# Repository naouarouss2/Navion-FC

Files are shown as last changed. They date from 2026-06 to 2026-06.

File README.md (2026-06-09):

# Navion FC

## What is it
It is a small all-in-one flight controller used for autonomous vehicles.

It will run Ardupilot and is compatible with any type of autonomous vehicles.

## Features ✅
-  Barometer
-  IMU
-  Magnometer
-  10 PWM outputs
-  PPM/SBUS input
-  4 Neopixel outputs
-  MicroSD Card Reader
-  USB-C Connector
-  SWD Debugging Interface
-  3 UART Headers
-  1 USART Header
-  1 I²C Header
-  Safety Switch Header
-  16MB External Flash
-  Battery Voltage Monitoring
-  Up to 40V battery input voltage
## Why do I want to make it ? 🛠️

I have always been passionate about autonomous vehicles and wanted to build a universal solution that can run all of the vehicles I'll be building in the future.

That's why I made my flight controller extremely modular and versatile.

## How does it work ?

-  You attach all of your ESCs and Servos to the PWM outputs.

-  Attach neopixel strips to the top neopixel headers (You should power them externally).

-  Connect a standard Pixhawk 2.4.8 (or similar) GPS module (You need to swap the connectors for JST-XH connectors) to the GPS and I²C headers.

-  Connect the battery to the battery header.

-  Connect the RC receiver to the PPM/SBUS header (and configure it accordingly later).

-  Connect a telemetry module to the USART2 header.

-  You can connect other UART accessories like a Lidar to the UART2 and UART3 headers.

-  Then you configure your peripherals in **Mission Planner**, setup your flight controller, plan a mission, and you should be good to go !

## PCB 

### Schematic



### Routing



### 3D View



## 3D Deisgn 🎨





## Firmware

This flight controller will run a custom ported version of the **[Ardupilot firmware](https://github.com/ArduPilot/ardupilot)**

## Disclaimer ⚠️

This project is still untested.

## Credits ❤️
Project made by : **Oussama NAOUAR**

Total logged working hours : **40 hrs**

Made as part of the **Hack Club Fallout** program.

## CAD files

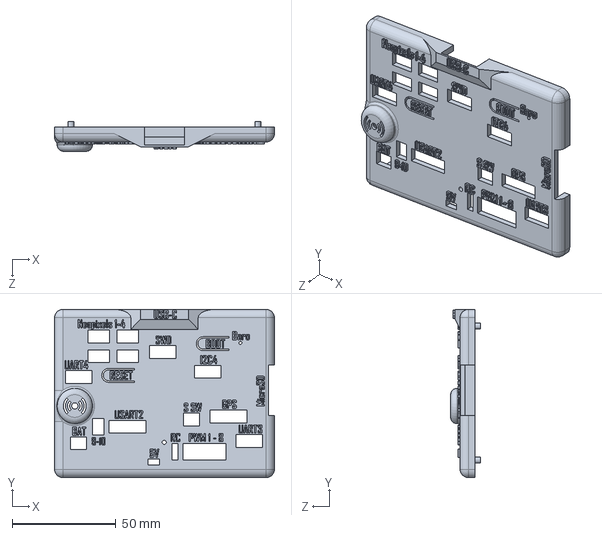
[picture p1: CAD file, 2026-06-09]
3D Printed Case/SolidWorks Files/Upper part.SLDPRT
106.0 x 81.0 x 14.3 mm

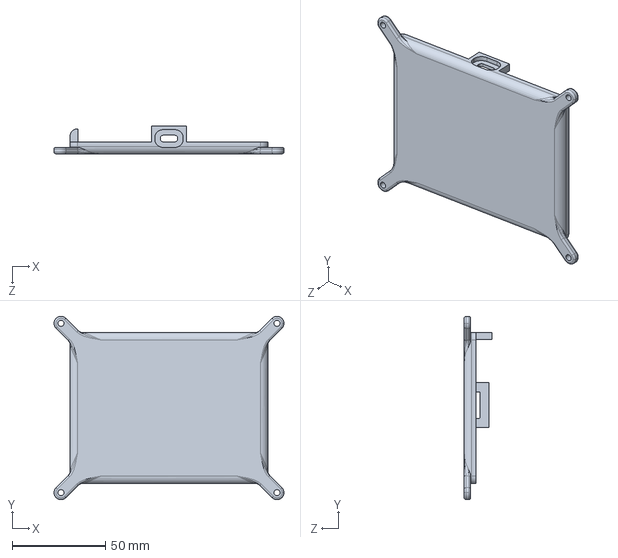
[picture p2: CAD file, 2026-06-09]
3D Printed Case/STEP Files/Lower part.STEP
123.2 x 98.2 x 14.8 mm

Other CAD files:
3D Printed Case/SolidWorks Files/Lower part.SLDPRT

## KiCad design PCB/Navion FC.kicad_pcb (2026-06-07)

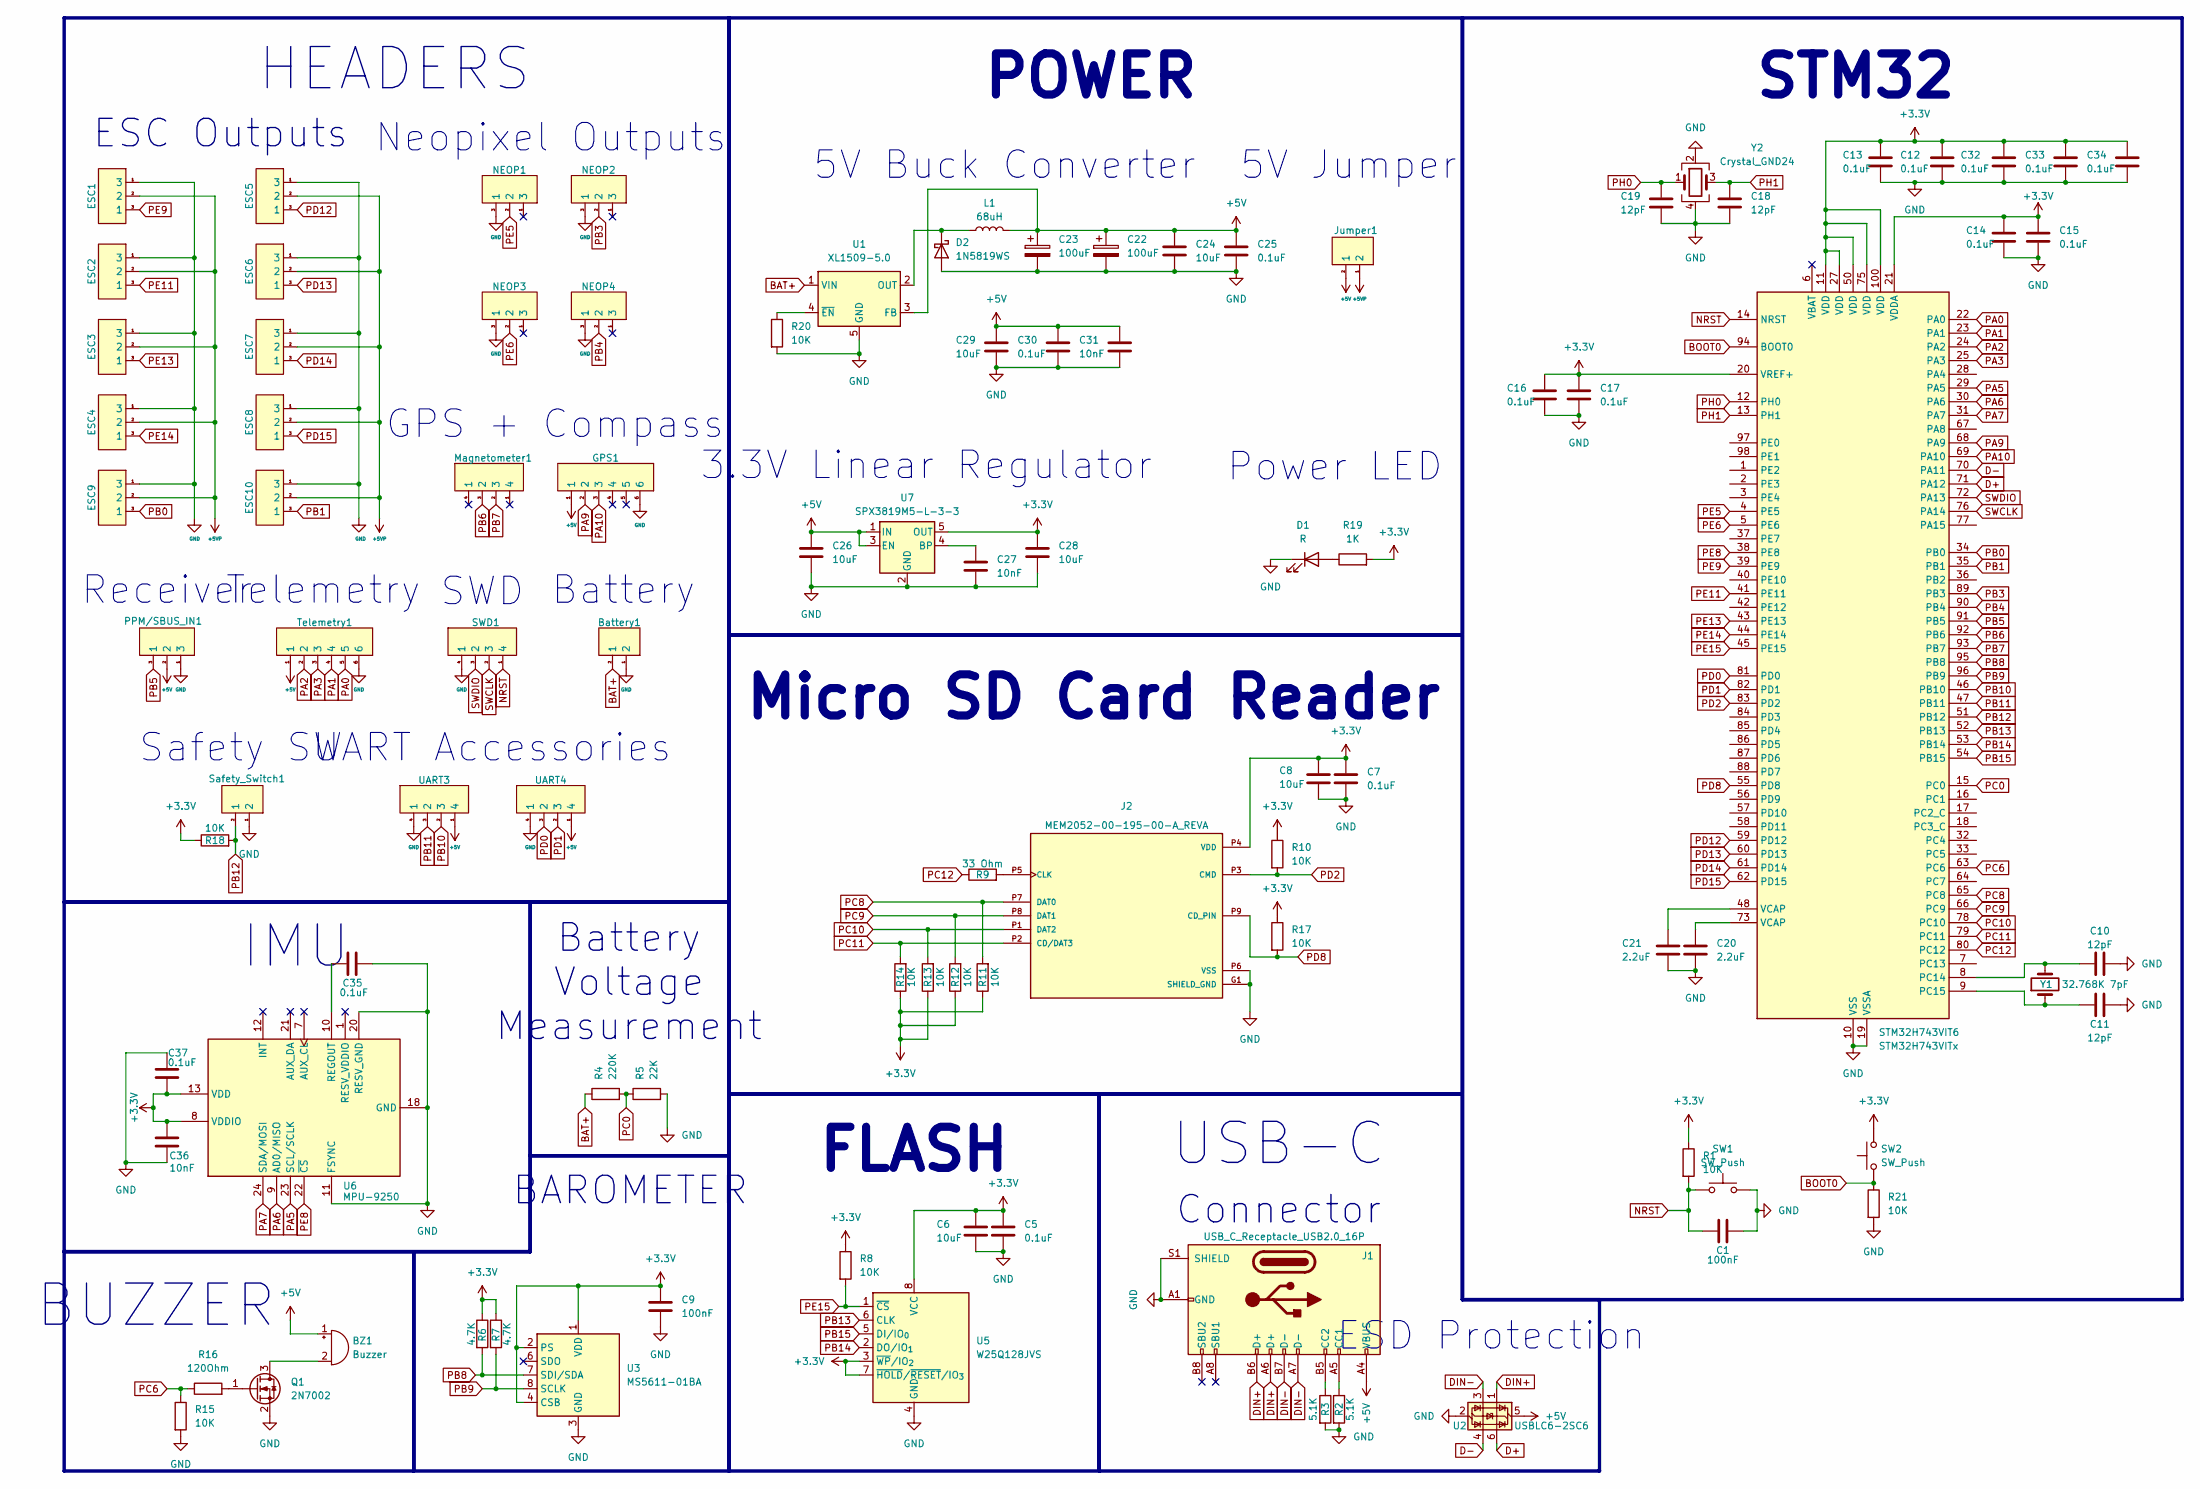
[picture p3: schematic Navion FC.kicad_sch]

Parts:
BZ1: Buzzer; Buzzer_12x9.5RM7.6
Battery1: JST_XH_B2B-XH-A_1x02_P2.50mm_Vertical
C1, C9: 100nF; C_0603_1608Metric
C5, C7, C12, C13, C14, C15, C16, C17, C25, C30, C32, C33, C34, C35, C37: 0.1uF; C_0603_1608Metric
C6, C8, C24, C26, C28, C29: 10uF; C_0603_1608Metric
C10, C11, C18, C19: 12pF; C_0603_1608Metric
C20, C21: 2.2uF; C_0603_1608Metric
C22, C23: 100uF; CP_EIA-3528-21_Kemet-B
C27, C31, C36: 10nF; C_0603_1608Metric
D1: R; LED_0603_1608Metric
D2: 1N5819WS; D_SOD-323
ESC1, ESC2, ESC3, ESC4, ESC5, ESC6, ESC7, ESC8, ESC9, ESC10: PinHeader_1x03_P2.54mm_Vertical
GPS1: JST_XH_B6B-XH-A_1x06_P2.50mm_Vertical
J1: USB_C_Receptacle_USB2.0_16P; USB_C_Receptacle_HCTL_HC-TYPE-C-16P-01A
J2: MEM2052-00-195-00-A_REVA; GCT_MEM2052-00-195-00-A_REVA; PARTREV A
Jumper1: PinHeader_1x02_P2.54mm_Vertical
L1: 68uH; L_Sunlord_SWPA8040S
Magnetometer1: JST_XH_B4B-XH-A_1x04_P2.50mm_Vertical
NEOP1, NEOP2, NEOP3, NEOP4: JST_XH_B3B-XH-A_1x03_P2.50mm_Vertical
PPM/SBUS_IN1: PinHeader_1x03_P2.54mm_Vertical
Q1: 2N7002; SOT-23
R1, R8, R10, R11, R12, R13, R14, R15, R17, R18, R20, R21: 10K; R_0603_1608Metric
R2, R3: 5.1K; R_0603_1608Metric
R4: 220K; R_0603_1608Metric
R5: 22K; R_0603_1608Metric
R6, R7: 4.7K; R_0603_1608Metric
R9: 33 Ohm; R_0603_1608Metric
R16: 120Ohm; R_0603_1608Metric
R19: 1K; R_0603_1608Metric
STM32H743VIT6: STM32H743VITx; LQFP-100_14x14mm_P0.5mm
SW1, SW2: SW_Push; SW_PUSH_6mm
SWD1: JST_XH_B4B-XH-A_1x04_P2.50mm_Vertical
Safety_Switch1: JST_XH_B2B-XH-A_1x02_P2.50mm_Vertical
Telemetry1: JST_XH_B6B-XH-A_1x06_P2.50mm_Vertical
U1: XL1509-5.0; SOIC-8_3.9x4.9mm_P1.27mm
U2: USBLC6-2SC6; SOT-23-6
U3: MS5611-01BA; LGA-8_3x5mm_P1.25mm
U5: W25Q128JVS; SOIC-8_5.3x5.3mm_P1.27mm
U6: MPU-9250; InvenSense_QFN-24_3x3mm_P0.4mm
U7: SPX3819M5-L-3-3; SOT-23-5
UART3, UART4: JST_XH_B4B-XH-A_1x04_P2.50mm_Vertical
Y1: 32.768K 7pF; Crystal_SMD_3215-2Pin_3.2x1.5mm
Y2: Crystal_GND24; Crystal_SMD_3225-4Pin_3.2x2.5mm

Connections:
+3.3V: C5.1, C6.1, C7.1, C8.1, C9.1, C12.1, C13.1, C14.1, C15.1, C16.1, C17.1, C28.1, C32.1, C33.1, C34.1, C36.2, C37.1, J2.P4 (VDD), R1.1, R6.1, R7.1, R8.1, R10.1, R11.1, R12.1, R13.1, R14.1, R17.1, R18.1, R19.2, STM32H743VIT6.11 (VDD), STM32H743VIT6.20 (VREF+), STM32H743VIT6.21 (VDDA), STM32H743VIT6.27 (VDD), STM32H743VIT6.50 (VDD), STM32H743VIT6.75 (VDD), STM32H743VIT6.100 (VDD), SW2.2, U3.1 (VDD), U3.2 (PS), U3.4 (CSB), U3.5 (CSB), U5.3 (~WP/IO_{2}), U5.7 (~HOLD/~RESET/IO_{3}), U5.8 (VCC), U6.8 (VDDIO), U6.13 (VDD), U7.5 (OUT)
+5V: BZ1.1 (+), C22.1, C23.1, C24.1, C25.1, C26.1, C29.1, C30.1, C31.1, GPS1.1, J1.A4 (VBUS), J1.A9 (VBUS), J1.B4 (VBUS), J1.B9 (VBUS), Jumper1.2 (1), L1.2, PPM/SBUS_IN1.2, Telemetry1.1, U1.3 (FB), U2.5 (VBUS), U7.1 (IN), U7.3 (EN), UART3.1 (4), UART4.1 (4)
+5VP: ESC1.2, ESC2.2, ESC3.2, ESC4.2, ESC5.2, ESC6.2, ESC7.2, ESC8.2, ESC9.2, ESC10.2, Jumper1.1 (2)
BAT+: Battery1.2 (1), R4.1, U1.1 (VIN)
BOOT0: R21.1, STM32H743VIT6.94 (BOOT0), SW2.1
D+: STM32H743VIT6.71 (PA12), U2.6 (I/O1)
D-: STM32H743VIT6.70 (PA11), U2.4 (I/O2)
DIN+: J1.A6 (D+), J1.B6 (D+), U2.1 (I/O1)
DIN-: J1.A7 (D-), J1.B7 (D-), U2.3 (I/O2)
GND: Battery1.1 (2), C1.2, C5.2, C6.2, C7.2, C8.2, C9.2, C10.2, C11.2, C12.2, C13.2, C14.2, C15.2, C16.2, C17.2, C18.2, C19.2, C20.2, C21.2, C22.2, C23.2, C24.2, C25.2, C26.2, C27.2, C28.2, C29.2, C30.2, C31.2, C32.2, C33.2, C34.2, C35.2, C36.1, C37.2, D1.1 (K), D2.2 (A), ESC1.1 (3), ESC2.1 (3), ESC3.1 (3), ESC4.1 (3), ESC5.1 (3), ESC6.1 (3), ESC7.1 (3), ESC8.1 (3), ESC9.1 (3), ESC10.1 (3), GPS1.6, J1.A1 (GND), J1.A12 (GND), J1.B1 (GND), J1.B12 (GND), J1.S1 (SHIELD), J2.G1 (SHIELD_GND), J2.G2 (SHIELD_GND), J2.G3 (SHIELD_GND), J2.G4 (SHIELD_GND), J2.P6 (VSS), NEOP1.3 (1), NEOP2.3 (1), NEOP3.3 (1), NEOP4.3 (1), PPM/SBUS_IN1.1 (3), Q1.2 (S), R2.2, R3.2, R5.2, R15.2, R20.2, R21.2, STM32H743VIT6.10 (VSS), STM32H743VIT6.19 (VSSA), STM32H743VIT6.26 (VSS), STM32H743VIT6.49 (VSS), STM32H743VIT6.74 (VSS), STM32H743VIT6.99 (VSS), SW1.2, SWD1.4 (1), Safety_Switch1.1 (2), Telemetry1.6, U1.5 (GND), U1.6 (GND), U1.7 (GND), U1.8 (GND), U2.2 (GND), U3.3 (GND), U5.4 (GND), U6.11 (FSYNC), U6.18 (GND), U6.20 (RESV_GND), U7.2 (GND), UART3.4 (1), UART4.4 (1), Y2.2, Y2.4
NRST: C1.1, R1.2, STM32H743VIT6.14 (NRST), SW1.1, SWD1.1 (4)
unnamed: BZ1.2 (-), Q1.3 (D)
unnamed: C20.1, STM32H743VIT6.73 (VCAP)
unnamed: C21.1, STM32H743VIT6.48 (VCAP)
unnamed: D1.2 (A), R19.1
unnamed: D2.1 (K), L1.1, U1.2 (OUT)
unnamed: J1.A5 (CC1), R2.1
unnamed: J1.B5 (CC2), R3.1
unnamed: J2.P5 (CLK), R9.2
unnamed: Q1.1 (G), R16.2
unnamed: C10.1, STM32H743VIT6.8 (PC14), Y1.2
unnamed: C11.1, STM32H743VIT6.9 (PC15), Y1.1
unnamed: R20.1, U1.4 (~EN)
unnamed: C35.1, U6.10 (REGOUT)
unnamed: C27.1, U7.4 (BP)
PA0: STM32H743VIT6.22 (PA0), Telemetry1.5
PA1: STM32H743VIT6.23 (PA1), Telemetry1.4
PA2: STM32H743VIT6.24 (PA2), Telemetry1.2
PA3: STM32H743VIT6.25 (PA3), Telemetry1.3
PA5: STM32H743VIT6.29 (PA5), U6.23 (SCL/SCLK)
PA6: STM32H743VIT6.30 (PA6), U6.9 (AD0/MISO)
PA7: STM32H743VIT6.31 (PA7), U6.24 (SDA/MOSI)
PA9: GPS1.2, STM32H743VIT6.68 (PA9)
PA10: GPS1.3, STM32H743VIT6.69 (PA10)
PB0: ESC9.3 (1), STM32H743VIT6.34 (PB0)
PB1: ESC10.3 (1), STM32H743VIT6.35 (PB1)
PB3: NEOP2.2, STM32H743VIT6.89 (PB3)
PB4: NEOP4.2, STM32H743VIT6.90 (PB4)
PB5: PPM/SBUS_IN1.3 (1), STM32H743VIT6.91 (PB5)
PB6: Magnetometer1.3 (2), STM32H743VIT6.92 (PB6)
PB7: Magnetometer1.2 (3), STM32H743VIT6.93 (PB7)
PB8: R6.2, STM32H743VIT6.95 (PB8), U3.7 (SDI/SDA)
PB9: R7.2, STM32H743VIT6.96 (PB9), U3.8 (SCLK)
PB10: STM32H743VIT6.46 (PB10), UART3.2 (3)
PB11: STM32H743VIT6.47 (PB11), UART3.3 (2)
PB12: R18.2, STM32H743VIT6.51 (PB12), Safety_Switch1.2 (1)
PB13: STM32H743VIT6.52 (PB13), U5.6 (CLK)
PB14: STM32H743VIT6.53 (PB14), U5.2 (DO/IO_{1})
PB15: STM32H743VIT6.54 (PB15), U5.5 (DI/IO_{0})
PC0: R4.2, R5.1, STM32H743VIT6.15 (PC0)
PC6: R15.1, R16.1, STM32H743VIT6.63 (PC6)
PC8: J2.P7 (DAT0), R11.2, STM32H743VIT6.65 (PC8)
PC9: J2.P8 (DAT1), R12.2, STM32H743VIT6.66 (PC9)
PC10: J2.P1 (DAT2), R13.2, STM32H743VIT6.78 (PC10)
PC11: J2.P2 (CD/DAT3), R14.2, STM32H743VIT6.79 (PC11)
PC12: R9.1, STM32H743VIT6.80 (PC12)
PD0: STM32H743VIT6.81 (PD0), UART4.3 (2)
PD1: STM32H743VIT6.82 (PD1), UART4.2 (3)
PD2: J2.P3 (CMD), R10.2, STM32H743VIT6.83 (PD2)
PD8: J2.P9 (CD_PIN), R17.2, STM32H743VIT6.55 (PD8)
PD12: ESC5.3 (1), STM32H743VIT6.59 (PD12)
PD13: ESC6.3 (1), STM32H743VIT6.60 (PD13)
PD14: ESC7.3 (1), STM32H743VIT6.61 (PD14)
PD15: ESC8.3 (1), STM32H743VIT6.62 (PD15)
PE5: NEOP1.2, STM32H743VIT6.4 (PE5)
PE6: NEOP3.2, STM32H743VIT6.5 (PE6)
PE8: STM32H743VIT6.38 (PE8), U6.22 (~CS)
PE9: ESC1.3 (1), STM32H743VIT6.39 (PE9)
PE11: ESC2.3 (1), STM32H743VIT6.41 (PE11)
PE13: ESC3.3 (1), STM32H743VIT6.43 (PE13)
PE14: ESC4.3 (1), STM32H743VIT6.44 (PE14)
PE15: R8.2, STM32H743VIT6.45 (PE15), U5.1 (~CS)
PH0: C19.1, STM32H743VIT6.12 (PH0), Y2.1
PH1: C18.1, STM32H743VIT6.13 (PH1), Y2.3
SWCLK: STM32H743VIT6.76 (PA14), SWD1.2 (3)
SWDIO: STM32H743VIT6.72 (PA13), SWD1.3 (2)

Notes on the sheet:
3.3V Linear Regulator
5V Jumper
UART Accessories
Receiver
Power LED
FLASH
Telemetry
GPS + Compass
BUZZER
STM32
Micro SD Card Reader
ESC Outputs
Neopixel Outputs
5V Buck Converter
Battery
BAROMETER
Safety SW
USB-C
IMU
POWER
HEADERS
Battery Voltage Measurement
Connector
ESD Protection
SWD

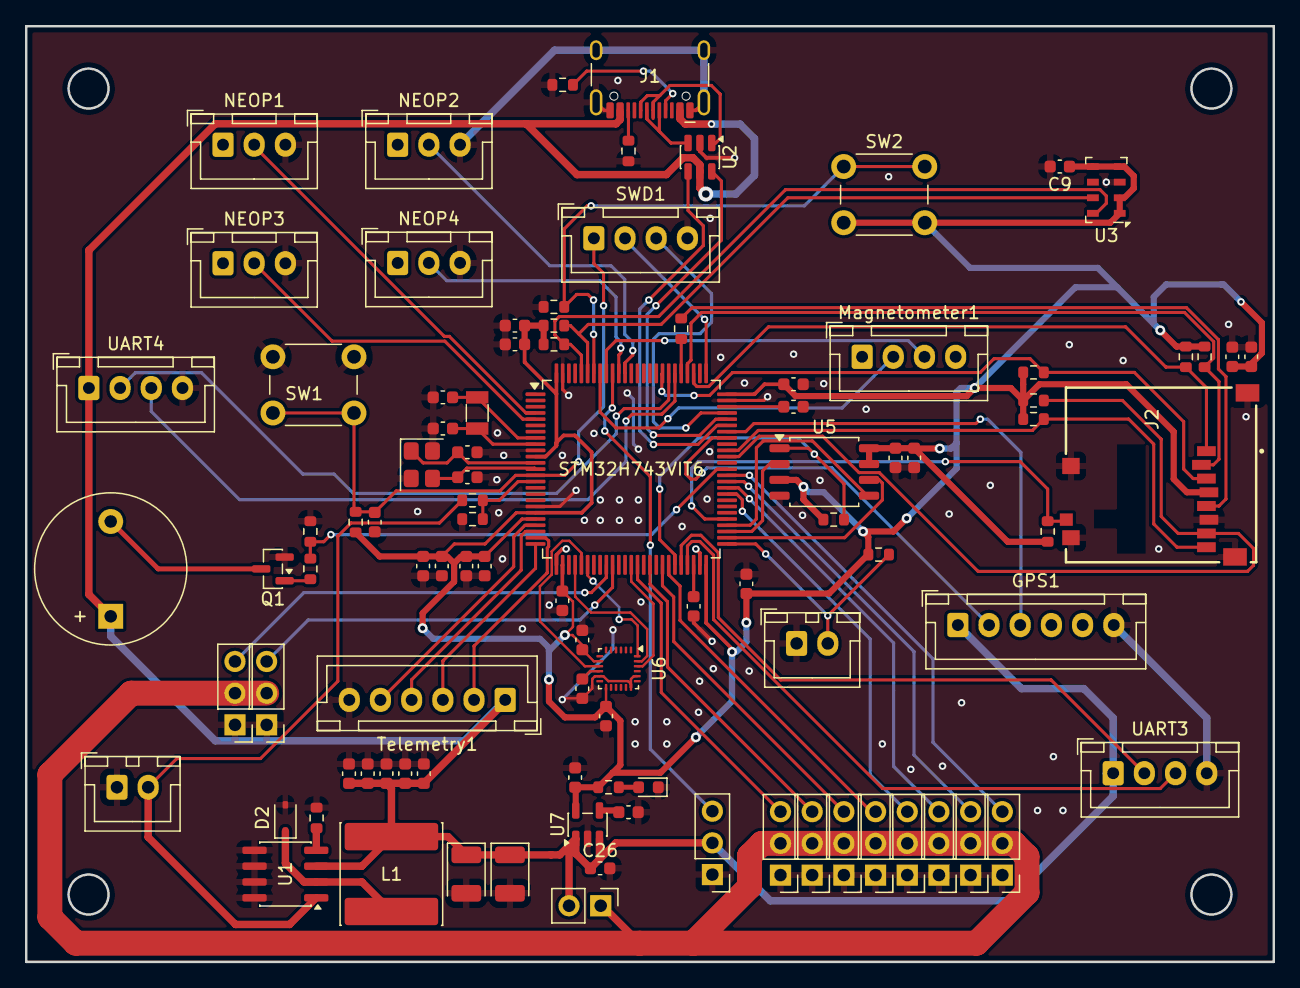
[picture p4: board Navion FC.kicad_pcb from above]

Board: 4 copper layers, 100.0 x 75.0 mm, 97 parts (0 on the bottom side), 76 nets.

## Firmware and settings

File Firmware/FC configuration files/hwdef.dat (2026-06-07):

# MCU class and specific type
MCU STM32H7xx STM32H743xx

# board ID. See Tools/AP_Bootloader/board_types.txt
APJ_BOARD_ID 9999

# ChibiOS system timer
STM32_ST_USE_TIMER 5
define CH_CFG_ST_RESOLUTION 16

# flash size
FLASH_SIZE_KB 2048
FLASH_RESERVE_START_KB 128

define HAL_STORAGE_SIZE 32768
STORAGE_FLASH_PAGE 14

# default to all pins low to avoid ESD issues
DEFAULTGPIO OUTPUT LOW PULLDOWN

# order of UARTs (and USB)
SERIAL_ORDER  OTG1 USART1 USART2 UART3 UART 4

# USB
PA11 OTG_FS_DM OTG1
PA12 OTG_FS_DP OTG1

# GPS1/Serial1
PA9  USART1_TX USART1
PA10 USART1_RX USART1

# Telemetry1/Serial2
PA2  USART2_TX USART2
PA3 USART2_RX USART2
PA0 USART1_CTS USART2
PA1 USART1_RTS USART2

# Serial3
PB10  UART3_TX UART3
PB11  UART3_RX UART3

# Serial4
PD1  UART4_TX UART4
PD0  UART4_RX UART4

# Serial5/Receiver
PB5 UART5_RX UART5

PC0 BATT_VOLTAGE_SENS ADC1 SCALE(1)

# SWD
PA13 JTMS-SWDIO SWD
PA14 JTCK-SWCLK SWD

# order of I2C buses
I2C_ORDER I2C4 I2C1

# I2C4/Magnetometer
PB6 I2C4_SCL I2C4
PB7 I2C4_SDA I2C4

# I2C1/Barometer
PB8 I2C1_SCL I2C1
PB9 I2C1_SDA I2C1

# SPI1/IMU
PA5 SPI1_SCK SPI1
PA6 SPI1_MISO SPI1
PA7 SPI1_MOSI SPI1
PE8 MPU_CS CS

# SPI2/Flash
PB13 SPI2_SCK  SPI2
PB14 SPI2_MISO SPI2
PB15 SPI2_MOSI SPI2
PE15 FLASH_CS CS

# PWM output for buzzer
PC6 TIM3_CH1 TIM3 GPIO(77) ALARM

# microSD Card Reader
PC12 SDMMC1_CK  SDMMC1
PD2  SDMMC1_CMD SDMMC1
PC8  SDMMC1_D0  SDMMC1
PC9  SDMMC1_D1  SDMMC1
PC10 SDMMC1_D2  SDMMC1
PC11 SDMMC1_D3  SDMMC1
PD8 SD_CARD_DETECT INPUT PULLUP

# PWM Outputs
PE9 TIM1_CH1 TIM1 PWM(1) GPIO(50)
PE11 TIM1_CH2 TIM1 PWM(2) GPIO(51)
PE13 TIM1_CH3 TIM1 PWM(3) GPIO(52)
PE14 TIM1_CH4 TIM1 PWM(4) GPIO(53)
PD12 TIM4_CH1 TIM4 PWM(5) GPIO(54)
PD13 TIM4_CH2 TIM4 PWM(6) GPIO(55)
PD14 TIM4_CH3 TIM4 PWM(7) GPIO(56)
PD15 TIM4_CH4 TIM4 PWM(8) GPIO(57)
PB0 TIM3_CH3 TIM3 PWM(9) GPIO(58)
PB1 TIM3_CH4 TIM3 PWM(10) GPIO(59)
PE5 TIM15_CH1 TIM15 PWM(11) GPIO(60)
PB3 TIM2_CH2 TIM2 PWM(12) GPIO(61)
PE6 TIM15_CH2 TIM15 PWM(13) GPIO(62)
PB4 TIM3_CH1 TIM3 PWM(14) GPIO(63)

SPIDEV mpu9250        SPI1 DEVID4  MPU_CS       MODE3  4*MHZ  8*MHZ
SPIDEV flash SPI2 DEVID1 FLASH_CS MODE3 16*MHZ 24*MHZ

BARO MS5611 I2C:1:0x76

# Compass declaration
COMPASS AK8963:probe_mpu9250 0 ROTATION_NONE
COMPASS HMC5883 I2C:4 ROTATION_NONE

define HAL_LOGGING_DATAFLASH
define HAL_LOGGING_SIZE 16384

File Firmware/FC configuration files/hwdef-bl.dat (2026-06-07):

# MCU class and specific type
MCU STM32H7xx STM32H743xx

# board ID. See Tools/AP_Bootloader/board_types.txt
APJ_BOARD_ID 9999

# crystal frequency
OSCILLATOR_HZ 8000000

# flash size
FLASH_SIZE_KB 2048

# bootloader is installed at zero offset
FLASH_RESERVE_START_KB 0

# the location where the bootloader will put the firmware
FLASH_BOOTLOADER_LOAD_KB 128



# order of UARTs (and USB)
SERIAL_ORDER OTG1

# USB
PA11 OTG_FS_DM OTG1
PA12 OTG_FS_DP OTG1

# pins for SWD debugging
PA13 JTMS-SWDIO SWD
PA14 JTCK-SWCLK SWD

# CS pins
PE8 MPU_CS CS
PE15 FLASH_CS CS

# microSD support
PC12 SDMMC1_CK  SDMMC1
PD2  SDMMC1_CMD SDMMC1
PC8  SDMMC1_D0  SDMMC1
PC9  SDMMC1_D1  SDMMC1
PC10 SDMMC1_D2  SDMMC1
PC11 SDMMC1_D3  SDMMC1

# enable FAT filesystem support (needs a microSD defined via SDMMC)
define HAL_OS_FATFS_IO 1

define AP_BOOTLOADER_FLASH_FROM_SD_ENABLED 1

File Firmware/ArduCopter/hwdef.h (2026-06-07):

/*
 generated hardware definitions from hwdef.dat - DO NOT EDIT
*/

#pragma once

#ifndef TRUE
#define TRUE 1
#endif

#ifndef FALSE
#define FALSE 0
#endif

#define MHZ (1000U*1000U)
#define KHZ (1000U)


#define AP_SIGNED_FIRMWARE 0

#define HAL_ENABLE_DFU_BOOT FALSE
#define CHIBIOS_BOARD_NAME "Navion_FC"
// MCU type (ChibiOS define)
#define STM32H7xx_MCUCONF
#define STM32H743_MCUCONF

#define STM32H743xx

// crystal frequency
#define STM32_HSECLK 8000000U

// UART used for stdout (printf)
// SDMMC available, enable POSIX filesystem support
#define USE_POSIX
#define HAL_USE_FATFS TRUE

#define HAL_OS_POSIX_IO TRUE

#define HAL_USE_SDC TRUE
#define STM32_SDC_USE_SDMMC1 TRUE
#define HAL_USE_SDMMC 1
#define STM32_USB_USE_OTG1                  TRUE
#define STM32_OTG2_IS_OTG1                  FALSE
#define HAL_USE_USB TRUE
#define HAL_USE_SERIAL_USB TRUE
#ifndef HAL_HAVE_HARDWARE_DOUBLE
#define HAL_HAVE_HARDWARE_DOUBLE 1
#endif
#ifndef HAL_WITH_MCU_MONITORING
#define HAL_WITH_MCU_MONITORING 1
#endif
#ifndef STM32H7
#define STM32H7 1
#endif
#define HAL_USE_HW_RNG TRUE
#define HAL_PROCESS_STACK_SIZE 0x1C00
#define HAL_OS_FATFS_IO 1
#define AP_BOOTLOADER_FLASH_FROM_SD_ENABLED 1
#define HAL_NUM_CAN_IFACES 0
#undef HAL_ENABLE_DRONECAN_DRIVERS
#define HAL_ENABLE_DRONECAN_DRIVERS 0
#define BOARD_FLASH_SIZE 2048

// location of loaded firmware
#define FLASH_LOAD_ADDRESS 0x08000000
#define EXT_FLASH_SIZE_MB 0
#define EXT_FLASH_RESERVE_START_KB 0
#define EXT_FLASH_RESERVE_END_KB 0
#define CRT0_AREAS_NUMBER 1
#define __EXTFLASHFUNC__
#define STORAGE_FLASH_START_PAGE 14
#ifndef AP_CRASHDUMP_ENABLED
#define AP_CRASHDUMP_ENABLED 0
#endif
#define FLASH_BOOTLOADER_LOAD_KB 128
#define FLASH_RESERVE_END_KB 256
#define APP_START_OFFSET_KB 0

#define HAL_RAM0_START 0x20000000
// memory regions
#define HAL_MEMORY_REGIONS {(void*)0x20000000, 0x00020000, 0x02 }, {(void*)0x30000000, 0x00040000, 0x08 }, {(void*)0x24000000, 0x00080000, 0x04 }, {(void*)0x00000400, 0x0000fc00, 0x02 }, {(void*)0x30040000, 0x00008000, 0x08 }, {(void*)0x38000000, 0x00010000, 0x01 }
#define HAL_CC_MEMORY_REGIONS {0x20000000, 0x20020000, CRASH_CATCHER_BYTE }, {0x30000000, 0x30040000, CRASH_CATCHER_BYTE }, {0x24000000, 0x24080000, CRASH_CATCHER_BYTE }, {0x00000400, 0x00010000, CRASH_CATCHER_BYTE }, {0x30040000, 0x30048000, CRASH_CATCHER_BYTE }, {0x38000000, 0x38010000, CRASH_CATCHER_BYTE }
#define HAL_MEMORY_TOTAL_KB 1055

// CPU serial number (12 bytes)
#define UDID_START UID_BASE


// APJ board ID (for bootloaders)
#define APJ_BOARD_ID 9999

#ifndef HAL_ENABLE_THREAD_STATISTICS
#define HAL_ENABLE_THREAD_STATISTICS FALSE
#endif
    
#ifndef HAL_HAVE_HARDWARE_DOUBLE
#define HAL_HAVE_HARDWARE_DOUBLE 0
#endif
#define HAL_EXPECTED_SYSCLOCK 400000000
#define HAL_EXPECTED_STM32_SYS_CK 400000000
#define HAL_EXPECTED_STM32_QSPICLK 200000000
#define HAL_EXPECTED_STM32_SDMMC1CLK 80000000
#define HAL_EXPECTED_STM32_SPI45CLK 100000000
#define HAL_EXPECTED_STM32_FDCANCLK 80000000

#define HAL_BOOTLOADER_BUILD TRUE
#define HAL_USE_ADC FALSE
#define HAL_NO_PRINTF
#define HAL_USE_I2C FALSE
#define HAL_USE_PWM FALSE
#define CH_DBG_ENABLE_STACK_CHECK FALSE
// avoid timer and RCIN threads to save memory
#define HAL_NO_TIMER_THREAD
#define HAL_NO_RCOUT_THREAD
#ifndef HAL_RCIN_THREAD_ENABLED
#define HAL_RCIN_THREAD_ENABLED 0
#endif
#ifndef AP_HAL_SHARED_DMA_ENABLED
#define AP_HAL_SHARED_DMA_ENABLED 0
#endif
#define HAL_NO_ROMFS_SUPPORT TRUE
#define CH_CFG_USE_TM FALSE
#ifndef CH_CFG_USE_REGISTRY
#define CH_CFG_USE_REGISTRY FALSE
#endif
#ifndef CH_CFG_USE_WAITEXIT
#define CH_CFG_USE_WAITEXIT FALSE
#endif
#ifndef CH_CFG_USE_MEMPOOLS
#define CH_CFG_USE_MEMPOOLS FALSE
#endif
#define CH_DBG_FILL_THREADS FALSE
#ifndef CH_CFG_USE_MUTEXES
#define CH_CFG_USE_MUTEXES FALSE
#endif
#ifndef CH_CFG_USE_EVENTS
#define CH_CFG_USE_EVENTS FALSE
#endif
#define CH_CFG_USE_EVENTS_TIMEOUT FALSE
#define CH_CFG_OPTIMIZE_SPEED FALSE
#define HAL_USE_EMPTY_STORAGE 1
#ifndef HAL_STORAGE_SIZE
#define HAL_STORAGE_SIZE 16384
#endif
#define HAL_USE_RTC FALSE
#ifndef CH_CFG_USE_DYNAMIC
#define CH_CFG_USE_DYNAMIC FALSE
#endif
#define STM32_FLASH_DISABLE_ISR 0
#ifndef PAL_USE_CALLBACKS
#define PAL_USE_CALLBACKS FALSE
#endif

#undef HAL_FLASH_PROTECTION
#define HAL_FLASH_PROTECTION 0
#define HAL_USE_SPI FALSE
// ADC config
#define HAL_ANALOG_PINS \


// GPIO config
// full pin define list
#define HAL_GPIO_PIN_FLASH_CS             PAL_LINE(GPIOE,15U)
#define HAL_GPIO_PIN_JTCK_SWCLK           PAL_LINE(GPIOA,14U)
#define HAL_GPIO_PIN_JTMS_SWDIO           PAL_LINE(GPIOA,13U)
#define HAL_GPIO_PIN_MPU_CS               PAL_LINE(GPIOE,8U)
#define HAL_GPIO_PIN_OTG_FS_DM            PAL_LINE(GPIOA,11U)
#define HAL_GPIO_PIN_OTG_FS_DP            PAL_LINE(GPIOA,12U)
#define HAL_GPIO_PIN_SDMMC1_CK            PAL_LINE(GPIOC,12U)
#define HAL_GPIO_PIN_SDMMC1_CMD           PAL_LINE(GPIOD,2U)
#define HAL_GPIO_PIN_SDMMC1_D0            PAL_LINE(GPIOC,8U)
#define HAL_GPIO_PIN_SDMMC1_D1            PAL_LINE(GPIOC,9U)
#define HAL_GPIO_PIN_SDMMC1_D2            PAL_LINE(GPIOC,10U)
#define HAL_GPIO_PIN_SDMMC1_D3            PAL_LINE(GPIOC,11U)

// peripherals enabled
#define AP_PARAM_DEFAULTS_FILE_PARSING_ENABLED 0


// auto-generated DMA mapping from dma_resolver.py

// Mask of DMA streams which are shared
#define SHARED_DMA_MASK 0


// generated UART DMA configuration lines


// generated SPI DMA configuration lines

// UART configuration
#define BOOTLOADER_DEV_LIST (BaseChannel *)&SDU1

#ifndef HAL_USE_SERIAL
#define HAL_USE_SERIAL FALSE
#endif
// USB configuration
#define HAL_USB_VENDOR_ID 0x1209
#define HAL_USB_PRODUCT_ID 0x5741
#define HAL_USB_STRING_MANUFACTURER "ArduPilot"
#define HAL_USB_STRING_PRODUCT "%BOARD%-BL"
#define HAL_USB_STRING_SERIAL "%SERIAL%"



/*
* I/O ports initial setup, this configuration is established soon after reset
* in the initialization code.
* Please refer to the STM32 Reference Manual for details.
*/
#define PIN_MODE_INPUT(n)           (0U << ((n) * 2U))
#define PIN_MODE_OUTPUT(n)          (1U << ((n) * 2U))
#define PIN_MODE_ALTERNATE(n)       (2U << ((n) * 2U))
#define PIN_MODE_ANALOG(n)          (3U << ((n) * 2U))
#define PIN_ODR_LOW(n)              (0U << (n))
#define PIN_ODR_HIGH(n)             (1U << (n))
#define PIN_OTYPE_PUSHPULL(n)       (0U << (n))
#define PIN_OTYPE_OPENDRAIN(n)      (1U << (n))
#define PIN_OSPEED_VERYLOW(n)       (0U << ((n) * 2U))
#define PIN_OSPEED_LOW(n)           (1U << ((n) * 2U))
#define PIN_OSPEED_MEDIUM(n)        (2U << ((n) * 2U))
#define PIN_OSPEED_HIGH(n)          (3U << ((n) * 2U))
#define PIN_PUPDR_FLOATING(n)       (0U << ((n) * 2U))
#define PIN_PUPDR_PULLUP(n)         (1U << ((n) * 2U))
#define PIN_PUPDR_PULLDOWN(n)       (2U << ((n) * 2U))
#define PIN_AFIO_AF(n, v)           ((v) << (((n) % 8U) * 4U))

/* PORTA:
 PA11 OTG_FS_DM OTG1 AF10
 PA12 OTG_FS_DP OTG1 AF10
 PA13 JTMS-SWDIO SWD AF0
 PA14 JTCK-SWCLK SWD AF0
*/
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

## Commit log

2026-06-07 Add README
    [Navion FC.kicad_pcb, Navion FC.kicad_sch]
2026-06-09 Update README with Navion FC details
    Added detailed information about the Navion FC flight controller, including features, purpose, PCB design, and firmware.
2026-06-09 Update README with connection instructions for peripherals
    Added instructions for connecting ESCs, servos, GPS, and other peripherals to the flight controller.
